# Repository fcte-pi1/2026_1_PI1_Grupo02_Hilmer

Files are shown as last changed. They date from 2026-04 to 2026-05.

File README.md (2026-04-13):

# Template PI1

Esse é o _template_ de repositório para ser utilizado pelos grupos de PI1 para organizar seu projeto. O _template_ é dividido em pastas, onde cada parte do projeto deve ser armazenada. Os arquivos a serem armazenados incluem documentação, código-fonte, arquivos de CAD, esquemáticos, arquivos de simulação de circuitos, e dados.

A organização e a correta utilização do repositório do projeto serão considerados na avaliação do grupo. Dessa forma, recomenda-se que *todos os membros* do grupo leiam as instruções deste repositório, aprendam a a utilizar o git (caso ainda não saibam) e também que o grupo combine uma estratégia de como irão utilizar o repositório em conjunto. Dessa forma não deixem de utilizar todas as ferramentas que o GitHub oferece, incluindo branchs, PRs, revisões, issues, calendários, dentre outros.

Lembrem sempre de evitar enviar arquivos muito grandes (>5MB). No caso de vídeos e outros arquivos pesados que são necessários, armazenar o arquivo em outra plataforma e colocar aqui apenas o _link_.

> [!IMPORTANT]
> A estrutura de pastas do projeto não reflete a divisão de equipes. Os membros podem e devem trabalhar nas diferentes pastas a depender da necessidade do projeto.

## Utilização

1. Crie o repositório do projeto utilizando a nomenclatura padrão no formato: `<ano>.<semestre>_PI1_Grupo<n>_<professor>`. Como um exemplo, um nome formado corretamente seria `2026.1_PI1_Grupo1_Diogo`. 

2. Crie uma equipe do projeto com a mesma nomenclatura do repositório porém com o sufixo `_Equipe`, como `2026.1_PI1_Grupo1_Diogo_Equipe`, e solicite, caso necessário, que a equipe tenha permissão de escrita no repositório do projeto.

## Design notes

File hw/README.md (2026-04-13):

# _Hardware_

Esta pasta deverá armazenar arquivos referentes a:

- Simulações de circuitos eletrônicos (alimentação, sensores, atuadores etc.): [Qucs](https://qucs.sourceforge.net/), [QSPICE](https://www.qorvo.com/design-hub/design-tools/interactive/qspice), [Fritzing](https://fritzing.org/), dentre outros.
- Esquemáticos de circuitos: [KiCad](https://www.kicad.org/), Qucs, QSPICE.
- Diagramas de bloco: [Canva](https://www.canva.com/pt_br/), [TikZ](https://tikz.net/).
- _Datasheets_ de componentes eletrônicos, microcontroladores, _shields_ Arduino, motores etc.
- Testes tabelados de circuitos: arquivos CSV, Excel.
- Imagens PNG e JPEG de resultados práticos: fotos de testes reais, gráficos de resultados etc.
- Outros arquivos referentes ao _hardware_ do projeto.

> [!WARNING]
> **Não acrescente código-fonte a esta pasta.** O código desenvolvido para microcontroladores e SOCs ([Arduino](https://www.arduino.cc/), [ESP32](https://www.espressif.com/), [Raspberry Pi](https://www.raspberrypi.com/)) deverá ser armazenado na pasta [src/firmware](https://github.com/fcte-pi1/template/tree/main/src/firmware) deste repositório.

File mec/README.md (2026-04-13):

# _Mecânica e Estruturas_

Esta pasta deverá ser utilizada para armazenar arquivos relativos ao projeto estrutural, mecanismos, materiais, estudos aerodinâmicos, equações dinâmicas, construção e manufatura, impressão 3D, e correlatos.

Os arquivos a serem incluídos, são, dentre outros:
- Arquivos CAD de peças e montagens (FCStd, STEP, etc). 
- Desenhos técnicos (pdf, etc).
- Arquivos de impressão 3D (STL, etc).
- Imagens rasterizadas e vetorizadas (eps, pdf, svg, etc).
- Documentos e estudos realizados para o projeto (markdown, LaTeX, etc).

Durante o projeto, os grupos são encorajados a realizarem estudos para o projeto de estruturas, mecanismos, aerodinamica, dentre outros, e muitos desses estudos não caberão no relatório a ser entregue. Esses estudos podem ser colocados também nessa pasta, preferencialmente utilizando markdown (.md) para facilitar a leitura em ambiente web. Lembre-se que você pode utilizar equações em formato LaTeX no markdown e não deixe de utilizar links para o material de referencia que utilizaram. Estudos bem realizados contarão de maneira positiva na avaliação das equipes, porém lembre-se que não é permitida a utilização de IA, e que esse material deve ser principalmente útil à equipe.

> [!WARNING]
> Não acrecente arquivos da parte de hardware eletrônico aqui, como arquivos de KiCAD. Estes devem ser salvos na pasta [hw](https://github.com/fcte-pi1/template/tree/main/hw) deste repositório.

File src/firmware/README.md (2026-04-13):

# _Firmware_
Esta pasta deverá armazenar arquivos referentes a:

- Código-fonte para microcontroladores e SOCs: [Arduino](https://www.arduino.cc/), [ESP32](https://www.espressif.com/), [Raspberry Pi](https://www.raspberrypi.com/), dentre outros.
- Projetos de organização destes códigos, caso utilize IDEs: [Arduino IDE](https://www.arduino.cc/en/software/), [Visual Studio](https://visualstudio.microsoft.com/pt-br/downloads/) etc.
- Arquivos de configuração: ```CMakeLists.txt``` se for usar [CMake](https://cmake.org/download/), ```Makefile``` se for usar [make](https://www.cs.colby.edu/maxwell/courses/tutorials/maketutor/) etc.

Evite incluir:
- Artefatos de compilação: os arquivos de saída compilados (binários, arquivos objeto, .hex, .elf) devem ser gerados pelo processo de compilação e não incluídos no repositório.
- Arquivos temporários/específicos do sistema operacional: Arquivos como .DS_Store (macOS) ou arquivos de configuração do editor (a menos que esteja usando uma configuração compartilhada como .editorconfig).
- Configurações pessoais: Arquivos de configuração locais específicos da máquina do desenvolvedor.

> [!WARNING]
> **Não acrescente arquivos referentes a _hardware_ nesta pasta.** Eles deverão ser armazenados na pasta [hw](https://github.com/fcte-pi1/template/tree/main/hw) deste repositório.

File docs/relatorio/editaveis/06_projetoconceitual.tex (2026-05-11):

\chapter{Projeto Conceitual do Produto}

\section{Características gerais}

\textcolor{red}{Descrever produto de forma geral. Apresentar itens teóricos sobre o projeto a serem aprofundados ou detalhados oportunamente.}

\textcolor{red}{Apresentar e explicar a Estrutura Analítica do Projeto (EAP), tomando cuidado com a legibilidade da imagem. Se necessário, coloque a EAP dentro do comando ``\textsf{\textbackslash begin\{landscape\} \textbackslash end\{landscape\}}'' para que ela seja apresentada em uma página deitada.}

\section{Estrutura}

\textcolor{red}{Apresentar desenho em CAD, indicar dimensões por lado/aresta/cota, indicar materiais utilizados e explicar o desenho e as decisões de projeto.}

\section{Descrição de \textit{hardware}}

\textcolor{red}{A descrição de \textit{hardware} no documento deve permitir que outras pessoas repliquem o produto proposto neste documento. Para isso, deve-se explicar de forma textual os principais sub-sistemas e as escolhas de projeto, além de indicar:}

\begin{itemize}
    \item \textcolor{red}{ O diagrama de blocos \cite{blockdiagram}, que oferece uma visão geral do hardware, com as principais partes do sistema e as ligações entre elas.}
    %\item A lista de materiais \cite{bom}, que facilita a montagem do sistema, indicando tudo que deve ser adquirido. Aproveitem a lista de materiais para apresentarem o orçamento dos mesmos.
    \item \textcolor{red}{ O esquemático \cite{esquematico}, que mostra as conexões elétricas entre os componentes. Deve-se indicar os componentes por nomes e símbolos, e as conexões entre eles, incluindo a pinagem dos componentes. Se o esquemático ficar muito grande, pode-se separa-lo em vários esquemáticos. A ligação em \textit{protoboard} não é considerada um esquemático adequado.}
\end{itemize}

\textcolor{red}{A Fig. \ref{fig:diagrama_blocos_e_esquematico} apresenta o diagrama de blocos e o esquemático de um circuito conversor de corrente alternada para corrente direta, a título de exemplo. Repare que o diagrama de blocos indica os subsistemas do circuito completo apresentado no esquemático.
% Comecem com o diagrama de blocos, que é mais genérico, e depois indiquem os detalhes com a lista de materiais e os esquemáticos.
}

\begin{figure}
    \centering
    
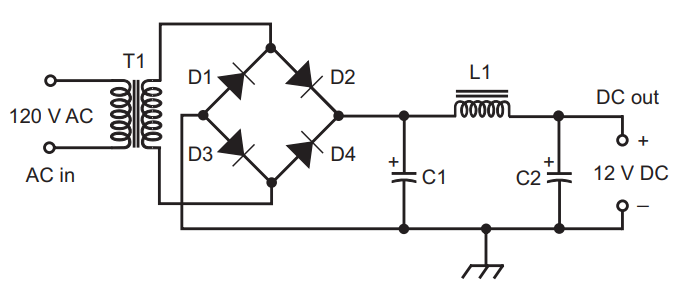
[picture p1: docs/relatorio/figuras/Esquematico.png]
    
    \caption{\textcolor{red}{Diagrama de blocos e esquemático de um circuito conversor de corrente alternada para corrente direta. Extraído de \cite{block_n_schematic}.}}
    \label{fig:diagrama_blocos_e_esquematico}
\end{figure}

\section{Análise de consumo energético}

\subsection{Identificação dos Subsistemas Elétricos}
\label{sec:identificacao_subsistemas}

A identificação dos subsistemas elétricos foi realizada com base nos componentes que consumirão energia durante a operação do micromouse, incluindo sensores, microcontroladores, atuadores, módulos de armazenamento e circuitos de suporte. Para fins de dimensionamento, foi adotado um tempo estimado de uso de 7200\,s, correspondente a uma missão de aproximadamente 2 horas. Os valores de tensão e corrente média foram obtidos a partir de \textit{datasheets} sempre que disponíveis, ou por estimativas conservadoras baseadas em condições realistas de operação.

\begin{table}[htbp]
    \centering
    \caption{Identificação dos subsistemas elétricos e parâmetros de operação}
    \label{tab:subsistemas_eletricos}

    \renewcommand{\arraystretch}{1.2}

    \begin{tabular}{lcccc}
        \hline
        \textbf{Componente} &
        \textbf{Qtde} &
        \textbf{Tensão (V)} &
        \textbf{Corrente média (mA)} &
        \textbf{Tempo (s)} \\
        \hline

        ESP32 & 1 & 3,3 & 200 & 7200 \\
        VL53L0X & 6 & 3,3 & 20 & 7200 \\
        Motor N20 (6V) & 2 & 6,0 & 400 & 7200 \\
        Driver (TB6612) & 1 & 3,3 & 30 & 7200 \\
        MPU6050 & 1 & 3,3 & 4 & 7200 \\
        INA226 & 1 & 3,3 & 0,33 & 7200 \\
        SD Reader & 1 & 3,3 & 80 & 7200 \\
        Regulador (MP1584EN) & 1 & 3,3 & 100 & 7200 \\
        Outros (LEDs, perdas) & -- & 3,3 & 100 & 7200 \\

        \hline
    \end{tabular}
\end{table}

Os valores apresentados na Tabela~\ref{tab:subsistemas_eletricos} contemplam os principais elementos energizados do sistema.

\subsection{Cálculo da Energia Consumida por Componente}
\label{sec:calculo_energia_componente}

A energia consumida por cada componente foi calculada por meio da expressão:

\begin{equation}
E = V \cdot I \cdot t
\end{equation}

em que $E$ representa a energia em joules, $V$ a tensão em volts, $I$ a corrente em ampères e $t$ o tempo de uso em segundos. Para os cálculos, as correntes em miliampères foram convertidas para ampères.

A seguir, apresenta-se o detalhamento da energia consumida por cada subsistema, cujos valores estão sintetizados na Tabela~\ref{tab:energia_por_componente}.

\begin{table}[htbp]
    \centering
    \caption{Energia consumida por componente}
    \label{tab:energia_por_componente}

    \renewcommand{\arraystretch}{1.2}

    \begin{tabular}{lc}
        \hline
        \textbf{Componente} & \textbf{Energia (J)} \\
        \hline

        ESP32 & 4752,00 \\
        VL53L0X & 2851,20 \\
        Motor N20 (2 unidades) & 34560,00 \\
        Driver (TB6612) & 712,80 \\
        MPU6050 & 95,04 \\
        INA226 & 7,84 \\
        SD Reader & 1900,80 \\
        Regulador (MP1584EN) & 2376,00 \\
        Outros (LEDs, perdas) & 2376,00 \\

        \hline
        \textbf{Total} & \textbf{49631,68} \\
        \hline
    \end{tabular}
\end{table}

\subsection{Estimativa do Consumo Total de Energia}
\label{sec:consumo_total_energia}

A energia total estimada por lançamento corresponde à soma das energias individuais dos subsistemas listados anteriormente:

\begin{equation}
E_{\text{total}}
=
4752{,}00 + 2851{,}20 + 34560{,}00 + 712{,}80 + 95{,}04 + 7{,}84 + 1900{,}80 + 2376{,}00 + 2376{,}00
\end{equation}

\begin{equation}
E_{\text{total}}
=
49631{,}68\,\mathrm{J}
\end{equation}

Para expressar esse consumo em watt-hora, utiliza-se a relação:

\begin{equation}
1\,\mathrm{Wh} = 3600\,\mathrm{J}
\end{equation}

Logo, a conversão do consumo total é dada por:

\begin{equation}
E_{\text{total,Wh}}
=
\frac{49631{,}68}{3600}
\approx
13{,}79\,\mathrm{Wh}
\end{equation}

Também é possível estimar a corrente média total do sistema a partir da soma das correntes nominais:

\begin{equation}
I_{\text{nom}}
=
200 + 120 + 800 + 30 + 4 + 0{,}33 + 80 + 100 + 100
=
1434{,}33\,\mathrm{mA}
\end{equation}

Portanto,

\begin{equation}
I_{\text{nom}}
\approx
1{,}434\,\mathrm{A}
\end{equation}

Para tornar o dimensionamento mais robusto, foi aplicada uma margem de segurança de 40\%, a fim de contemplar variações de carga, perdas não modeladas e oscilações durante a operação:

\begin{equation}
I_{\text{proj}}
=
I_{\text{nom}} \times 1{,}4
\end{equation}

Substituindo-se o valor obtido:

\begin{equation}
I_{\text{proj}}
=
1{,}434 \times 1{,}4
\approx
2{,}01\,\mathrm{A}
\end{equation}

Em seguida, considerou-se um fator de utilização de 70\%, uma vez que nem todos os subsistemas operam continuamente em máxima corrente durante toda a missão:

\begin{equation}
I_{\text{real}}
=
I_{\text{proj}} \times 0{,}7
\end{equation}

Assim,

\begin{equation}
I_{\text{real}}
=
2{,}01 \times 0{,}7
\approx
1{,}41\,\mathrm{A}
\end{equation}

A capacidade mínima da bateria pode ser estimada por:

\begin{equation}
C_{\text{min}}
=
I_{\text{real}} \times t
\end{equation}

Para uma autonomia de 2 horas:

\begin{equation}
C_{\text{min}}
=
1{,}41 \times 2
=
2{,}82\,\mathrm{Ah}
\approx
2820\,\mathrm{mAh}
\end{equation}

Para uma autonomia de 3 horas:

\begin{equation}
C_{\text{min}}
=
1{,}41 \times 3
=
4{,}23\,\mathrm{Ah}
\approx
4230\,\mathrm{mAh}
\end{equation}

\subsection{Escolha da Fonte de Alimentação}
\label{sec:escolha_fonte}

Com base no consumo energético total estimado, a demanda por lançamento é de aproximadamente 13,79\,Wh. Considerando uma margem de segurança adicional de 25\%, obtém-se uma demanda projetada de aproximadamente 17,24\,Wh.

\begin{equation}
E_{\text{proj,Wh}}
=
13{,}79 \times 1{,}25
\approx
17{,}24\,\mathrm{Wh}
\end{equation}

A fonte de alimentação selecionada é um conjunto formado por duas células idênticas em série do modelo N21700CG-50 da BAK Battery. Considerando as especificações típicas informadas, cada célula possui tensão nominal de 3,6\,V e capacidade de 5,0\,Ah. Em série, o conjunto passa a fornecer tensão nominal de 7,2\,V, mantendo a capacidade de 5,0\,Ah.

A energia nominal do conjunto é dada por:

\begin{equation}
E_{\text{bat}}
=
7{,}2 \times 5{,}0
=
36\,\mathrm{Wh}
\end{equation}

Esse valor é superior à demanda projetada de 17,24\,Wh, oferecendo folga energética suficiente para o funcionamento do robô.

Como os motores são nominais de 6\,V, o barramento principal será tratado como a alimentação de potência do sistema, enquanto os blocos de lógica, sensores e microcontrolador serão alimentados com tensão regulada pelo MP1584EN para 3,3\,V.

A tabela a seguir resume a escolha da fonte.

\begin{table}[htbp]
    \centering
    \caption{Resumo da fonte de alimentação selecionada}
    \label{tab:fonte_alimentacao}

    \renewcommand{\arraystretch}{1.2}

    \begin{tabular}{lccc}
        \hline
        \textbf{Fonte} & \textbf{Tensão nominal} & \textbf{Capacidade} & \textbf{Energia} \\
        \hline
        2 células em série & 7,2\,V & 5,0\,Ah & 36\,Wh \\
        \hline
    \end{tabular}
\end{table}

subsubsection{Síntese do dimensionamento}

Com base nos cálculos apresentados, o sistema possui consumo energético estimado de 49\,631,68\,J por lançamento, equivalente a aproximadamente 13,79\,Wh. Após aplicação de margem de segurança de 25\%, a demanda projetada passa a ser de aproximadamente 17,24\,Wh.

A fonte selecionada, composta por duas células em série, fornece aproximadamente 36\,Wh, o que atende confortavelmente à demanda do projeto. Dessa forma, a solução escolhida supre a necessidade energética do micromouse e oferece margem adequada para picos de corrente, perdas de conversão e variações operacionais.

Ressalta-se que a corrente dos motores foi considerada em regime nominal de operação, e não em condição de \textit{stall}, evitando superdimensionamento excessivo do sistema de alimentação.

\subsection{Planejamento do Circuito de Alimentação}
\label{sec:planejamento_circuito_alimentacao}

O circuito de alimentação será organizado em dois blocos: potência e lógica. O barramento principal, derivado das duas células em série, alimenta a etapa de potência, enquanto o regulador MP1584EN reduz a tensão para 3,3\,V na etapa lógica.

Para reduzir oscilações de tensão e interferências entre os subsistemas, serão adotadas as seguintes medidas:
\begin{itemize}
    \item uso de regulador buck para a linha de 3,3\,V;
    \item capacitores de desacoplamento próximos aos circuitos integrados;
    \item capacitor de bulk na entrada do sistema;
    \item separação física e elétrica entre alimentação dos motores e da lógica;
    \item uso do driver TB6612 como interface entre ESP32 e motores.
\end{itemize}

A INA226 será utilizada apenas para monitoração de corrente, tensão e potência, permitindo acompanhar o comportamento energético em tempo real. Assim, a estabilidade do sistema será garantida pela combinação entre regulação adequada, desacoplamento e separação das linhas de alimentação.

\section{Referências dos Datasheets}
\label{sec:referencias}

\begin{itemize}

    \item ESP32 -- Espressif Systems. \textit{ESP32 Series Datasheet}. Disponível em:
    \url{https://www.espressif.com/sites/default/files/documentation/esp32_datasheet_en.pdf}

    \item VL53L0X -- STMicroelectronics. \textit{VL53L0X Time-of-Flight Ranging Sensor Datasheet}. Disponível em:
    \url{https://www.st.com/resource/en/datasheet/vl53l0x.pdf}

    \item MPU6050 -- InvenSense. \textit{MPU-6000 and MPU-6050 Product Specification}. Disponível em:
    \url{https://invensense.tdk.com/wp-content/uploads/2015/02/MPU-6000-Datasheet1.pdf}

    \item TB6612FNG -- Toshiba. \textit{TB6612FNG Dual H-Bridge Motor Driver Datasheet}. Disponível em:
    \url{https://toshiba.semicon-storage.com/info/docget.jsp?did=10660}

    \item MP1584EN -- Monolithic Power Systems. \textit{MP1584 3A Step-Down Converter Datasheet}. Disponível em:
    \url{https://www.monolithicpower.com/en/documentview/productdocument/index/version/2/document_type/Datasheet/lang/en/sku/MP1584EN-LF-Z/document_id/221}

    \item INA226 -- Texas Instruments. \textit{INA226 Current/Power Monitor Datasheet}. Disponível em:
    \url{https://www.ti.com/lit/ds/symlink/ina226.pdf}

    \item BAK N21700CG-50 -- BAK Battery. \textit{Product Data Sheet}. Especificações consideradas: tensão nominal de 3,6\,V, capacidade típica de 5,0\,Ah, tensão máxima de carga de 4,2\,V, tensão final de descarga de 2,5\,V, corrente padrão de carga de 0,5C e corrente máxima de descarga de 3C.

    \item Motor N20 6V -- Especificações obtidas a partir do modelo comercial adquirido, complementadas por valores típicos de motores N20 equivalentes utilizados em aplicações embarcadas.

\end{itemize}

\section{Descrição de \textit{software}}

\textcolor{red}{Itens fundamentais:}

\begin{itemize}
    \item \textcolor{red}{ \textbf{Diagrama BPMN para entender o \textit{software} proposto:} deve deixar claro os principais atores do sistema, suas atividades (de negócios), insumos e resultados.}
    \item \textcolor{red}{\textbf{\textit{Backlog} funcional do \textit{software}:}}
    \begin{itemize}
        \item \textcolor{red}{ Escrito no formato de histórias de usuário ou casos de uso (decisão da equipe);}
        \item \textcolor{red}{ Ao declarar o \textit{backlog} de requisitos funcionais, usar a  classificação de MoSCoW (\textit{Must have}, \textit{Should have} e \textit{Could have}),  para um melhor entendimento do próprio \textit{backlog}.}
    \end{itemize}
    \item \textcolor{red}{\textbf{ \textit{Backlog} não-funcional do \textit{software}:}}
    \begin{itemize}
        \item \textcolor{red}{ Descrever os requisitos não-funcionais de forma objetiva;}
        \item \textcolor{red}{ Mais facilmente, mais rapidamente, são descrições subjetivas não-válidas. Um exemplo de requisito não-funcional de desempenho: ``a página deve carregar em até 5s quando em conexão 4G''. }
    \end{itemize}
    \item \textcolor{red}{ \textbf{Diagrama de casos de uso,} contendo os atores do sistema, os requisitos com os quais eles interagem e os tipos de relacionamentos entre requisitos realizados por um mesmo ator (ex.: \textit{include}, \textit{extend}). Obs.: este é um diagrama sobre requisitos funcionais.}
    \item \textcolor{red}{ \textbf{Descrição da arquitetura da solução de \textit{software} proposta:}}
    \begin{itemize}
        \item \textcolor{red}{ Propósito do \textit{software} (qual o seu papel no sistema);}
        \item \textcolor{red}{ Estilo arquitetural contendo:}
        \begin{itemize}
            \item \textcolor{red}{ Padrão adotado: MVC, MVP, Microsserviços, Monolítico, etc (Justificar);}
            \item \textcolor{red}{ Linguagens de programação: Java, Python, C\#, JavaScript, etc.}
            \item \textcolor{red}{ \textit{Frameworks} e bibliotecas: Spring Boot, .NET Core, React, Angular, Django, etc.}
            \item \textcolor{red}{ Banco de dados: Relacional (PostgreSQL, MySQL, etc) X NãoSQL (MongoDB,etc). }
        \end{itemize}
        \item \textcolor{red}{ Diagrama de alto nível: representação esquemática dos componentes da arquitetura, suas responsabilidades e comunicações, esclarecendo a composição do \textit{front-end} e do \textit{back-end}.}
    \end{itemize}
    \item \textcolor{red}{ \textbf{Persistência de dados:} diagrama de entidade relacionamento do banco de dados usado na solução proposta.}
    \item \textcolor{red}{ \textbf{Análise de dados:} as variáveis definidas nos requisitos do projeto em abordagem numérica e gráfica.}
    \item \textcolor{red}{ \textbf{Diagrama de estados} esclarecendo os estados assumidos pelo \textit{software} e os eventos que causam as mudanças de estado do \textit{software}.}
    \item \textcolor{red}{ \textbf{Protótipo funcional do \textit{software}, navegável.}}
    \item \textcolor{red}{\textbf{ Roteiro de testes funcionais:} }
    \begin{itemize}
        \item \textcolor{red}{Código do caso de teste;}
        \item \textcolor{red}{Nome do caso de teste;}
        \item \textcolor{red}{Tipo do caso de teste (unitário, integrado ou sistema);}
        \item \textcolor{red}{ Objetivo do caso de teste;}
        \item \textcolor{red}{ Pré-condições do sistema para o teste ser realizado;}
        \item \textcolor{red}{ Descrição dos procedimentos a serem executados para o teste;}
        \item \textcolor{red}{ Resultado esperado para o teste ser aprovado (pós-condição após realizado o teste);}
        \item \textcolor{red}{ Especificação do reparo a ser executado (caso o teste não seja aprovado);}
        \item \textcolor{red}{ Resultado após reparo (o caso do teste ser necessário de ser repetido após reparo).}
    \end{itemize}
\end{itemize}

% \textcolor{red}{Com relação ao \textit{software}, será necessário apresentar os seguintes itens: % pacotes de componentes de \textit{software}, suas funções e características, e explicar as decisões de projeto:
% \begin{enumerate}
%     \item Um diagrama do processo de negócio do problema que a máquina se propõe a resolver (BPNM) – não é UML, mas é fundamental para entender como o sistema se comporta como um todo, incluindo o usuário;
%     \item Lista de casos de uso (backlog do sistema). Backlog funcional;
%     \item Lista de requisitos não-funcionais a serem satisfeitos pelo sistema;
%     \item Diagrama de casos de uso: mostrando os requisitos funcionais, seus atores e como eles interagem entre si;
%     \item Diagrama de Classes: apresentando quais dados são manipulados pelo sistema (internamente e externamente – ex.: resultados de experimentos);
%     \item Diagrama de arquitetura, identificando todos os componentes da máquina e suas iterações com o software;
%     \item Diagrama de estados da máquina (sistema);
%     \item Descrição dos testes dos componentes da máquina e dos testes funcionais que deveriam ser feitos para avaliar o funcionamento da máquina e identificar defeitos. São importantes os testes unitários (componentes) e de integração (conjunto de componentes) e o roteiro de testes.
% \end{enumerate}
% }
%\textcolor{red}{Com relação ao \textit{software}, será necessário apresentar pacotes de componentes de \textit{software}, suas funções e características, e explicar as decisões de projeto.}

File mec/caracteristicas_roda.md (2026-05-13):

# Características da Roda e Pneu do Micromouse

## 1. Introdução

Nesse documento, estão descritas as características centrais e demais informações referentes ao modelo de roda (que inclui a roda interna e o pneu) selecionado para o projeto de micromouse, que possuirá duas rodas na parte de trás da carcaça e um deslizador (skid) na frente.

As características definidas foram baseadas em diversos fatores, os quais estão, em sua maioria, descritos na página [*Esboço de características desejáveis das rodas*](./mec/esboco_caracteristicas_desejaveis_rodas.md). Além disso, a escolha também foi influenciada pelo fato de integrantes da equipe se disporem a emprestar rodas que possuiam, com propriedades adequadas, para o projeto. Essa abordagem permite que o grupo corte o custo de compra das rodas, e dispensa o tempo necessário para a encomenda e entrega do produto.

<br>

## 2. Propriedades

### 2.1. Material

O pneu é composto de um **elastômero termoplástico (TPE)** chamado de **SBS** (*estireno-butadieno-estireno*). Esse material é conhecido pela sua flexibilidade, maciez e alta aderência, sendo essa última fundamental para o desejável alto atrito com o solo.

A roda interna, que já é moldada para o encaixe com o pneu, é feita de plástico  **ABS** (*Acrilonitrila Butadieno Estireno*), que possui boa durabilidade e resistência, além de sua leveza.

### 2.2. Dimensões

O pneu possui um diâmetro de *30 mm* e largura de *11 mm*. A roda interna, por sua vez, possui diâmetro de *17 mm* e largura de *7 mm*, além de um vão no seu eixo de 
diamêtro *4,5 mm*.

### 2.3. Textura da banda de rodagem

A textura da banda de rodagem é composta por uma linha central lisa com largura *1,94 mm*, e sulcos de comprimento *2,75 mm* em ambos os lados por toda a superfície.

Apesar de ser preferível uma superfície sem sulcos, para maximizar o atrito com a superfície lisa em *MDF*, a existência de sulcos não trará impactos negativos significantes para essa questão, dado o escopo e o contexto do projeto.

<br>

## 3. Desenhos Técnicos

Abaixo, estão apresentados os desenhos técnicos da roda interna e do pneu.

<p align="center"><i>Imagem 1:</i> Desenho técnico da Roda Interna</p>

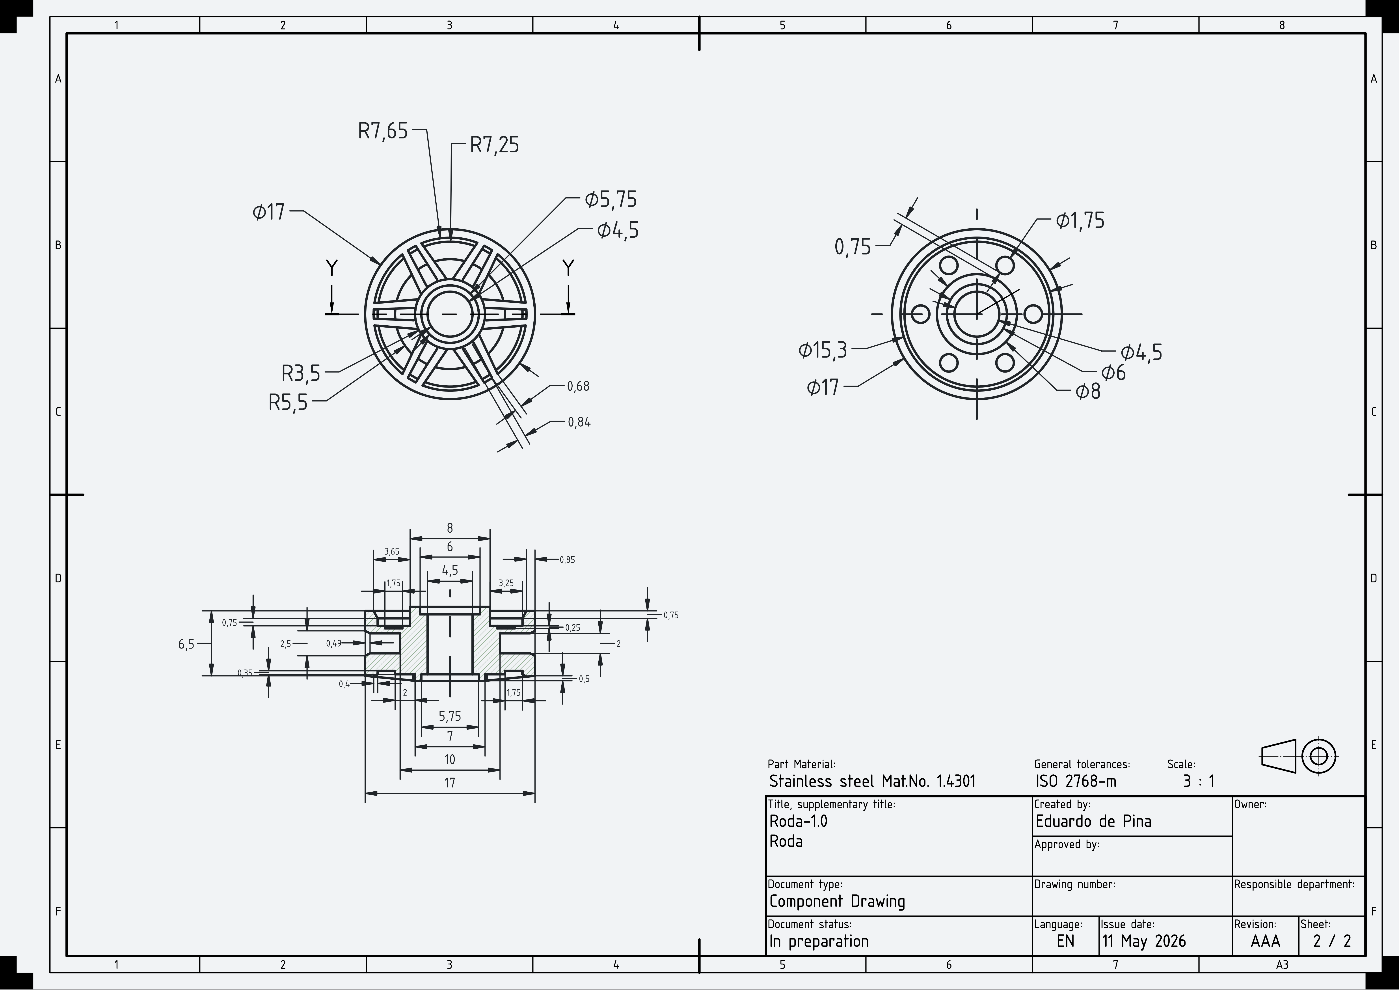
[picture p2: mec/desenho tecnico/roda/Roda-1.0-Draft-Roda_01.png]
Roda Interna


<p align="center"><b>Fonte: </b>Autoria de <a href="https://github.com/eduardodpms">Eduardo de Pina</a></p>

<br>

<p align="center"><i>Imagem 2:</i> Desenho técnico do Pneu</p>

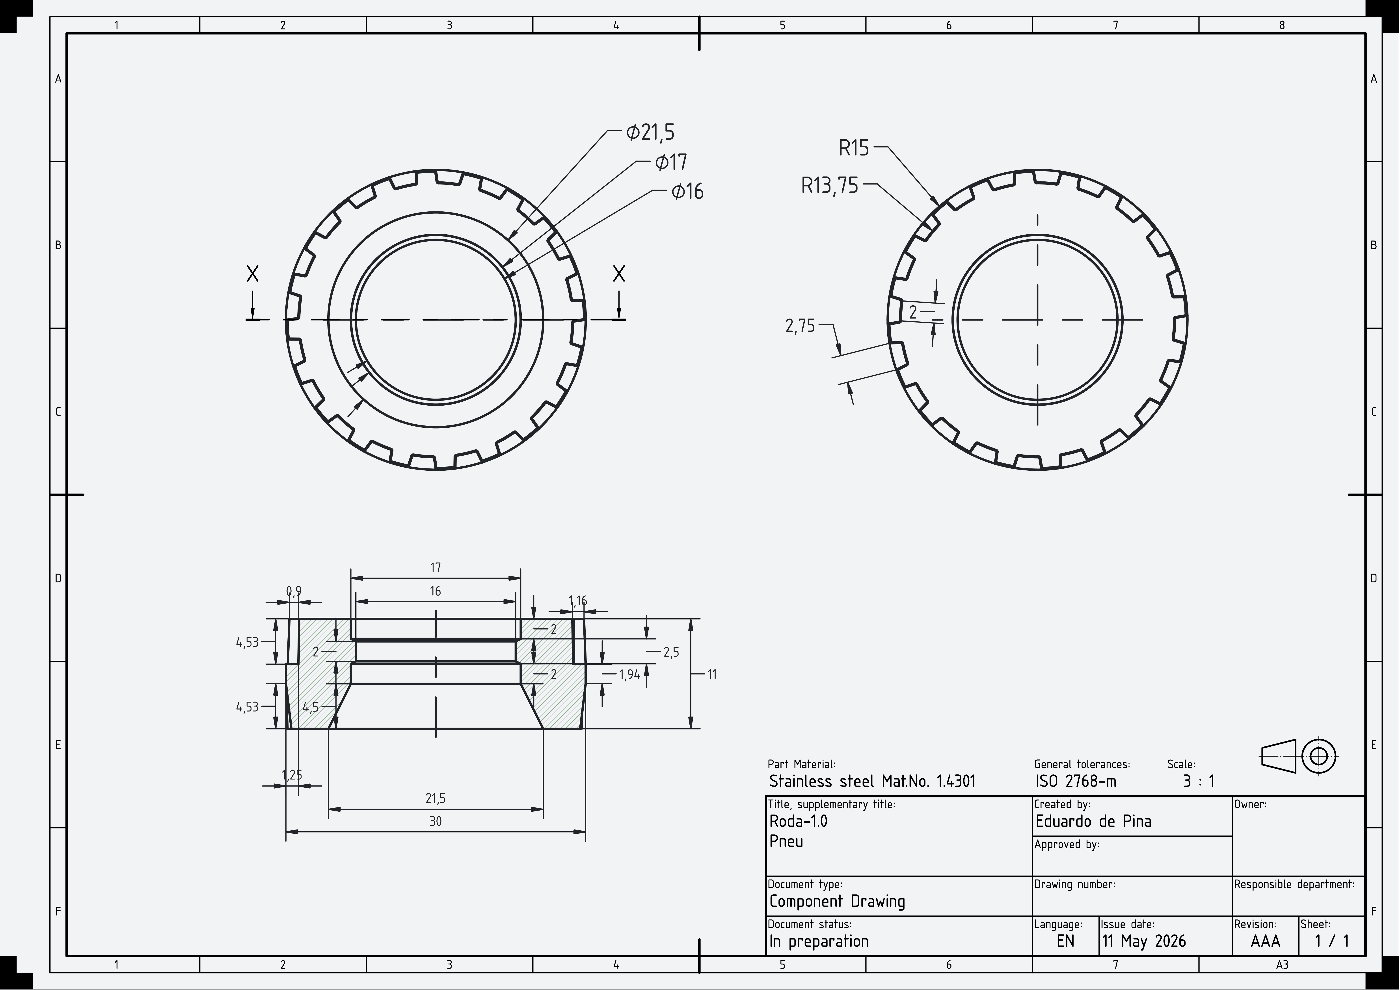
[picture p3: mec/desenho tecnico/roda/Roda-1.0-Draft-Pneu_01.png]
Pneu


<p align="center"><b>Fonte: </b>Autoria de <a href="https://github.com/eduardodpms">Eduardo de Pina</a></p>

<br>

## 4. Tabela de Versionamento

| Versão | Data | Autor | Descrição | Revisor |
| :-: | :-: | :-: | :-: | :-: |
| 1.0 | 12/05/2026 | [Eduardo de Pina](https://github.com/eduardodpms) | Criação do documento | [Giovanni Mateus](https://github.com/GiovanniMateus
) |

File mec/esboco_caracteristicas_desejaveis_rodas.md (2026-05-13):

# Esboço das características desejáveis das rodas

## 1. Introdução

Seguindo o modelo inicial de CAD para o robô desenvolvida pelo núcleo de estrutura e pesquisas direcionadas, foram discutidas medidas provisórias para serem utilizadas como base na seleção das rodas e pneus que serão utilizados no MicroMouse, buscando cumprir o objetivo da equipe.

<br>

## 2. CAD e Vãos

A base do modelo do robô está apresentada por meio de um CAD neste repositório. A imagem a seguir exibe, em vista tridimensional, uma captura de tela desse modelo.

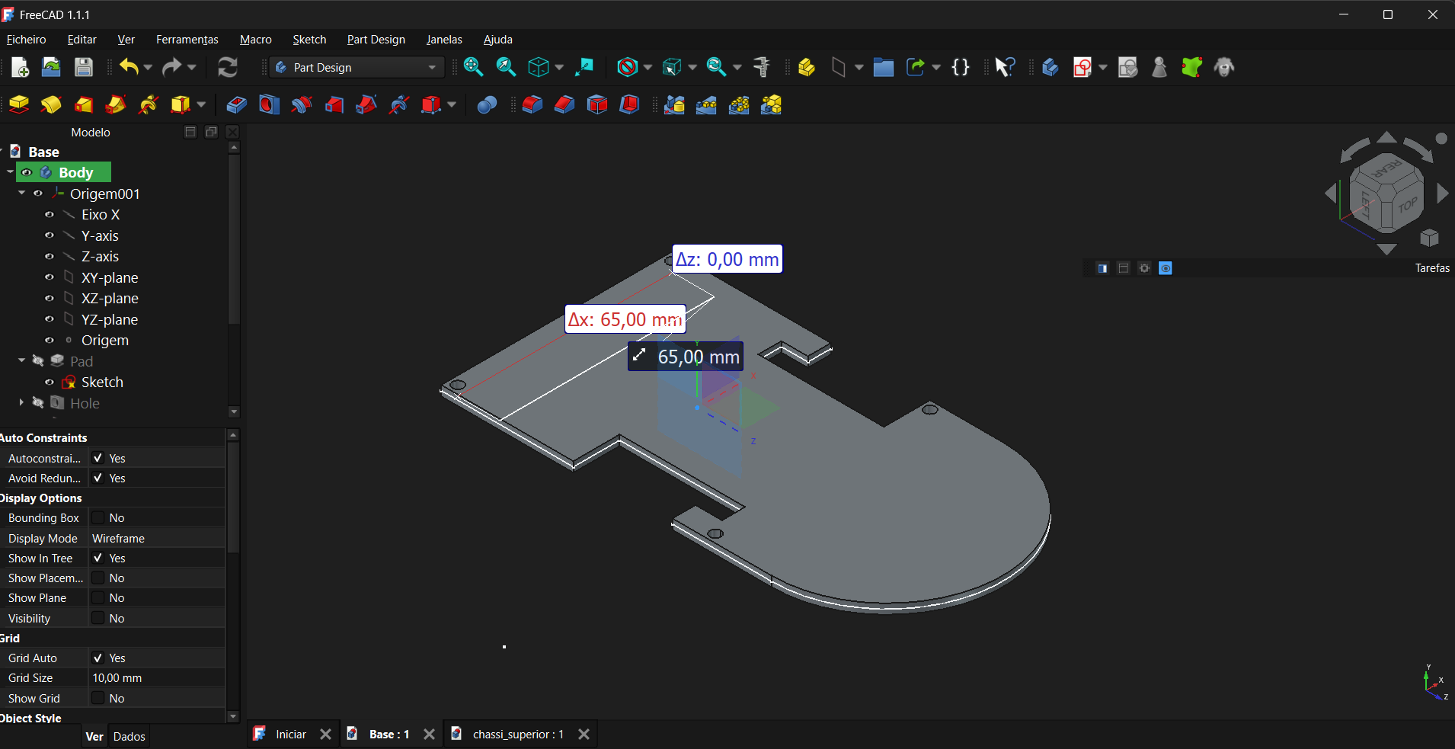
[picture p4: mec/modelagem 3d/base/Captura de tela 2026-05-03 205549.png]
CAD da Base


Os vãos destinados as rodas têm as dimensões de **30mm** x **14mm**, o que dá um direcionamento para a decisão da faixa de tamanhos possíveis para a roda.

<br>

## 3. Largura dos Pneus

A largura dos pneus, ou largura da banda de rodagem, é um fator que influencia diretamente na estabilidade do robô, assim como na precisão em curvas e no atrito com o solo. De forma resumida, para um *micromouse*, rodas mais finas proporcionam curvas mais precisas, enquanto rodas mais grossas proporcionam maior estabilidade para a estrutura como um todo, e maior área de contato do pneu com o solo, isto é, maior atrito.

Considerando o objetivo central da equipe, que não está focada em desenvolver um robô competitivo, e sim um robô estável, funcional, testável, e capaz de superar pequenos buracos de encaixe no labirinto, haverá uma preferência por rodas mais grossas (banda de rodagem > **1cm**). Além disso, há um espaço de **14mm** disponível para a roda no modelo inicial do chassi, o que não implica em um fator limitante para esse tamanho (já que uma parte do excesso pode extrapolar a largura do robô), mas dá um direcionamento nesse sentido.

Nesse sentido, a faixa ideal de largura da roda, seguindo o alinhamento da equipe, é de `11mm - 15mm`.

<br>

## 4. Diâmetro dos Pneus

O diâmetro dos pneus é outro fator decisivo na relação de escolha da roda. Rodas maiores tendem a fornecer maior velocidade em troca de mais torque, enquanto rodas menores tendem a fornecer mais precisão. Adicionalmente, aqui há um fator limitante para essa escolha: o comprimento do vão do chassi, que deve ser estritamente maior que o pneu para permitir a rolagem.

Para isso, será definida uma faixa de diâmetros de `20mm - 25mm`, que garantirá ao menos **5mm** de folga para a rolagem dos pneus, proporcionando também um tamanho que respeite a estrutura geral do *micromouse*.

<br>

## 5. Grip e Atrito

O *grip* é uma variável complexa que analisa fatores como [material](#6-material), textura e [largura dos pneus](#3-largura-dos-pneus), condições e material da pista para maximizar o atrito na superficie. Esse objetivo é central no desenvolvimento do projeto, uma vez que pneus sem atrito dificultam a previsibilidade e o cálculo dos movimentos do robô, além de também prejudicarem o controle sobre os mesmos.

Em relação às condições da pista, é esperado que a mesma seja construida sobre um material *mdf*, sem quantidades relevantes de umidade ou poeira, o que dispensa a necessidade de *sulcos* na banda de rodagem. Com relação à textura do material do pneu, o ideal seria um pneu liso, para maximizar o *grip* com o solo, mesmo essa abordagem tendendo a proporcionar maior desgaste do pneu com o tempo.

Nesse sentido, apesar de **preferível** que não haja textura na banda de rodagem, e existência de sulcos não impactará significativamente no atrito com o solo a ponto de prejudicar a equipe.

<br>

## 6. Material

Por fim, a respeito do material do pneu, é desejado um material macio e aderente. Para isso, é preferível alguma derivação de **borracha sintética**, como aquelas utilizadas nas peças de *Lego* (*SBS* e *SEBS*). Por fins de personalização, uma alternativa plástica seria o *filamento TPU*, utilizado em impressoras 3D.

<br>

## 7. Referências utilizadas

JAIN, J. **Robot Wheel Traction: Surface & Tire Type Selection Guide**. ZBOTIC. Disponível em: https://zbotic.in/robot-wheel-traction-surface-tire-type-selection-guide. Acesso em 4 maio 2026.

**How to choose proper Tires**. Micromouse USA. Disponível em: http://micromouseusa.com/?p=1111. Acesso em 4 maio 2026.

**What is The Role of Tire Size in Speed, Grip, and Stability?**. Brewminate. Disponível em: https://brewminate.com/what-is-the-role-of-tire-size-in-speed-grip-and-stability. Acesso em 4 maio 2026.

**De que são feitas as peças LEGO®?**. LEGO. Disponível em: https://www.lego.com/pt-br/service/help-topics/article/what-lego-bricks-are-made-of. Acesso em 4 maio 2026.

<br>

## 8. Tabela de Versionamento

| Versão | Data | Autor | Descrição | Revisor |
| :-: | :-: | :-: | :-: | :-: |
| 1.0 | 05/05/2026 | [Eduardo de Pina](https://github.com/eduardodpms) | Criação do documento | [Caio Venâncio](https://github.com/caio-venancio) |

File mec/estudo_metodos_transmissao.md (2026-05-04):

# Estudo sobre métodos de transmissão da roda no motor

## 1. Objetivo

Esta pesquisa compara métodos de  transmissão entre motor e roda para o micromouse, com foco em uma solução que seja simples de montar, confiável e adequada ao CAD do chassi.

## 2. Métodos avaliados

### 2.1 Roda direta no eixo do motor N20

Nesta opção, a roda é encaixada diretamente no eixo de saída do motor N20. Como o N20 já possui redução interna, o sistema fica mais simples:

```text
motor N20 com redução → roda encaixada diretamente no eixo
```

**Vantagens:**

- Menor quantidade de peças.
- Não precisa alinhar engrenagens externas.
- Não precisa tensionar correia.
- Menor chance de folga, travamento ou erro no CAD.
- Boa opção para garantir uma versão funcional do robô.

**Desvantagens:**

- Menor liberdade para alterar mecanicamente a relação de velocidade/torque.
- Se a roda for muito grande, o robô pode ficar rápido demais.
- Depende de encontrar roda compatível com eixo tipo D de 3 mm.

### 2.2 Engrenagens retas externas

Nesta opção, usa-se um pinhão pequeno no eixo do motor e uma engrenagem maior no eixo da roda:

```text
motor → pinhão pequeno → engrenagem maior → eixo da roda → roda
```

**Vantagens:**

- Permite aumentar o torque na roda.
- Permite reduzir a velocidade mecanicamente.
- Permite testar o chassi com um eixo de roda separado.
- É simples de explicar e pode ser fabricada ou comprada com peças de robótica.

**Desvantagens:**

- Exige alinhamento preciso entre pinhão, engrenagem maior e eixo da roda.
- Precisa de suporte para o eixo da roda, preferencialmente com bucha ou rolamento.
- Aumenta o número de peças e o risco de folga ou travamento.
- Os dois lados precisam ficar praticamente iguais para o robô não puxar para um lado.

### 2.3 Polias com correia GT2

Nesta opção, uma polia no motor transmite movimento para uma polia na roda usando correia dentada GT2:

```text
motor → polia pequena → correia GT2 → polia maior → eixo da roda → roda
```
**Vantagens:**

- transmissão mais suave e silenciosa;
- permite deixar o motor mais afastado da roda;
- reduz o contato direto entre engrenagens;
- permite alterar a relação de velocidade/torque trocando as polias;
- é comum em projetos de robótica e impressoras 3D.

**Desvantagens:**

- precisa de tensionamento correto da correia;
- se a correia ficar frouxa, pode pular dente;
- se ficar apertada demais, aumenta o atrito e pode forçar o motor;
- exige mais cuidado no CAD para prever ajuste de tensão;
- pode ocupar mais espaço no chassi.

---

## 3. Comparação das opções

| Critério | Roda direta no N20 | Engrenagens retas | Correia GT2 | Melhor para o grupo |
|---|---|---|---|---|
| Facilidade de montagem | Alta | Média | Média/baixa | Roda direta |
| Número de peças | Baixo | Médio | Médio/alto | Roda direta |
| Risco de desalinhamento | Baixo | Médio/alto | Médio | Roda direta |
| Ajuste de torque mecânico | Baixo | Bom | Bom | Engrenagens/GT2 |
| Necessidade de tensionamento | Não | Não | Sim | Roda direta/engrenagens |
| Chance de funcionar rápido | Alta | Média | Média/baixa | Roda direta |

---

## 4. Método escolhido: engrenagens retas

O método escolhido será a **transmissão por engrenagens retas**.

A ideia é usar:

- um **pinhão pequeno** no eixo do motor;
- uma **engrenagem maior** no eixo da roda.

Montagem básica:

```text
motor → pinhão pequeno → engrenagem maior → eixo da roda → roda
```

Esse método foi escolhido porque permite aumentar o torque, reduzir a velocidade e testar o chassi com um eixo de roda separado.

---

## 5. Como funciona

O motor gira o próprio eixo. O pinhão preso nesse eixo gira junto e movimenta a engrenagem maior. A engrenagem maior fica presa ao eixo da roda, fazendo a roda girar.

Etapas:

1. O motor gira.
2. O pinhão gira junto com o motor.
3. O pinhão move a engrenagem maior.
4. A engrenagem maior gira o eixo da roda.
5. O eixo gira a roda.

---

## 6. O que prever no CAD

O CAD precisa prever:

- posição dos dois motores;
- suporte firme para os motores;
- espaço para o pinhão;
- espaço para a engrenagem maior;
- furo ou suporte para o eixo da roda;
- bucha ou rolamento para o eixo;
- mesma distância e alinhamento nos dois lados do robô.

Como serão dois motores, a montagem deve ser simétrica:

```text
lado esquerdo: motor + pinhão + engrenagem + eixo + roda
lado direito: motor + pinhão + engrenagem + eixo + roda
```

---

## 7. Cálculos essenciais

### Relação de transmissão

```text
relação = dentes da engrenagem maior ÷ dentes do pinhão
```

Exemplo:

```text
pinhão = 10 dentes
engrenagem maior = 40 dentes

relação = 40 ÷ 10 = 4:1
```

Isso significa que o motor gira 4 voltas para a roda girar 1 volta. A roda fica mais lenta, mas com mais torque.

### RPM da roda

```text
RPM da roda = RPM do motor ÷ relação
```

Exemplo com motor de 750 RPM e relação 4:1:

```text
RPM da roda = 750 ÷ 4 = 187,5 RPM
```

---

## 8. Testes, riscos e conclusão

Antes de usar no robô completo, é necessário testar:

- se a roda gira sem travar;
- se o pinhão e a engrenagem estão alinhados;
- se não existe folga excessiva;
- se os dois lados giram de forma parecida;
- se o robô anda reto.

| Risco | Como evitar |
|---|---|
| Engrenagem travando | Ajustar distância entre motor e eixo da roda |
| Folga | Aproximar as engrenagens sem apertar demais |
| Robô andando torto | Usar peças e relações iguais nos dois lados |
| Atrito no eixo | Usar bucha ou rolamento |
| Motor desalinhando | Prender o motor com suporte firme |

---

## Referências rápidas

## Referências

CANADA ROBOTIX. N20 Micro Metal Gear Motor with Encoder. Disponível em: <https://www.canadarobotix.com/products/2846>. Acesso em: 2 maio 2026.

ROBOTSHOP. Aslong Motor DC 6V 750RPM 3mm Shaft Mini Metal Gearwheel Gear Motor N20 with Encoder Cable. Disponível em: <https://www.robotshop.com/products/aslong-motor-dc-6v-750rpm-3mm-shaft-mini-metal-gearwheel-gear-motor-n20-w-encoder-cable>. Acesso em: 2 maio 2026.

ROBOCORE. Micro Motor com Caixa de Redução 6V 750RPM com Encoder. Disponível em: <https://www.robocore.net/motor-motoredutor/micro-motor-caixa-de-reducao-6v-750rpm-com-encoder>. Acesso em: 2 maio 2026.

KHK GEARS. Gear technical reference: center distance. Disponível em: <https://khkgears.net/new/gear_knowledge/gear-nomenclature/center-distance.html>. Acesso em: 2 maio 2026.

SDP/SI. Timing belt and pulley technical information. Disponível em: <https://www.sdp-si.com/resources/elements-of-metric-gear-technology/index.php>. Acesso em: 2 maio 2026.

NSK. Bearing technical information. Disponível em: <https://www.nsk.com/products/bearings/>. Acesso em: 2 maio 2026.

UKMARS. UKMARSBot motor selection. Disponível em: <https://ukmars.org/projects/ukmarsbot/ukmarsbot-build-guide/motor-selection/>. Acesso em: 2 maio 2026.

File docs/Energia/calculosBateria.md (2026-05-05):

#  Estimativa de Consumo Energético

## Consumo nominal por componente

Valores baseados em datasheets (quando disponíveis) ou estimativas realistas de operação.

| Componente | Qtde | Corrente Unitária (mA) | Total (mA) | Fonte / Observação |
|---|---|---|---|---|
| ESP32 | 1 | 200 | 200 | Wi-Fi ativo típico |
| VL53L0X | 6 | 20 | 120 | Datasheet (~19mA típico) |
| Motor N20 (6V) | 2 | 400 | 800 | Operação com carga |
| Driver (DRV8833/TB6612) | 1 | 30 | 30 | Consumo interno |
| MPU6050 | 1 | 4 | 4 | Datasheet típico |
| SD Reader | 1 | 80 | 80 | Escrita moderada |
| Regulador (MP1584EN) | 1 | — | 100 | Perdas (~10%) |
| Outros (LEDs, perdas) | — | — | 100 | Margem técnica |

---

## Soma inicial

Corrente total nominal:

I_total = 200 + 120 + 800 + 30 + 4 + 80 + 100 + 100  
I_total ≈ 1434 mA ≈ 1.43 A

---

## Aplicação da margem de segurança

Considerando margem de 40% (variações operacionais e incertezas)

I_projeto = 1.43 A × 1.4  
I_projeto ≈ 2.00 A

---

##  Ajuste para uso real

Considerando fator de utilização de 70% (nem todos os componentes operam continuamente no máximo)

I_real = 2.00 A × 0.7  
I_real ≈ 1.40 A

---

## Cálculo da capacidade da bateria

### Para 2 horas de autonomia

Capacidade = 1.40 A × 2 h  
Capacidade ≈ 2.8 Ah ≈ 2800 mAh

---

### Para 3 horas de autonomia

Capacidade = 1.40 A × 3 h  
Capacidade ≈ 4.2 Ah ≈ 4200 mAh

---

## Resultado final

| Autonomia | Capacidade recomendada |
|---|---|
| 2 horas | 2500 – 3000 mAh |
| 3 horas | 4000 – 4500 mAh |

---

# Observação importante

A corrente dos motores foi considerada em regime nominal de operação e não em condição de stall, evitando superdimensionamento do sistema de energia.

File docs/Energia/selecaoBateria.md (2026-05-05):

# Componentes Necessários

## Baterias

### Pack Bateria Li-Ion 7,4V 2500mAh com BMS — R$ 67
Essa já vem toda montada, então não precisamos dos outros componentes caso a gente escolha ela.
[Ver produto](https://www.robocore.net/baterias-fontes/pack-bateria-li-ion-7_4v-2500mah-com-bms)

---

### Lishen LR2170 SA — R$ 15
**Especificações:** 21700 Li-ion, 3.6V, 4000mAh (12A) / 4500mAh (13.5A)
[Ver produto](https://www.alibaba.com/product-detail/2024-Grade-A-original-Lishen-LR2170SK_1601261306357.html)

> Não vamos considerar essa opção por causa do tempo de entrega nos sites disponíveis.

---

### Bateria 21700 3.7V 3000mAh Li-ion Recarregável c/ Proteção — Seven — R$ 30
**Especificações:** 21700, 3.7V, 3000mAh, com proteção, para lanterna e power bank
[Ver produto](https://m.magazineluiza.com.br/bateria-21700-3-7v-3000mah-li-ion-recarregavel-c-protecao-para-lanterna-e-power-bank-seven/p/ka5h0ggffb/cj/batr/)

---

### Bateria do Professor Renato — Sem custo
**Especificações:** Íon de lítio, 3.7V, 1500mAh
Baterias cedidas pelo laboratório do Professor Renato — opção escolhida pela equipe.

---

## Outros Componentes

| Componente | Preço Médio | Link |
|---|---|---|
| Jumper (Macho-Macho x40) | R$ 7,50 – R$ 19 | [Robocore](https://www.robocore.net/cabo/jumpers-macho-macho-x40-cabos) |
| Fita Isolante | R$ 5 | [Mercado Livre](https://www.mercadolivre.com.br/lorenzetti-10m-x-19mm-fita-isolante-antichama-proteco-para-fios-cor-preta/p/MLB28067596) |
| Conector JST PH 2 vias | R$ 15 – R$ 30 | [Mercado Livre](https://www.mercadolivre.com.br/mini-conector-jst-ph-2-vias-passo-20mm-05-conjuntos/up/MLBU1160212662) |
| Estanho para solda | R$ 10 | [Mercado Livre](https://www.mercadolivre.com.br/estanho-para-solda-40x60-080mm-tubo-10g/up/MLBU1764209073) |
| BMS 2S 20A 7,4V | R$ 20 | [Mercado Livre](https://www.mercadolivre.com.br/placa-bms-2s-20a-74v-cbalanceamento/up/MLBU3217754090) |
| Mini Carregador Lítio 2S | R$ 38 | [Robocore](https://www.robocore.net/baterias-fontes/mini-carregador-bateria-litio-2s) |

---

## Orçamentos

### Se o Professor Renato puder dar as baterias

**Opção recarregável:**
- Jumper + Fita Isolante + Estanho + Conector + BMS + Carregador
- **Total: R$ 19 + R$ 5 + R$ 10 + R$ 30 + R$ 20 + R$ 38 = R$ 122**

**Opção não recarregável:**
- Jumper + Fita Isolante + Estanho + Conector + BMS (x2 kits)
- **Total: (R$ 19 + R$ 5 + R$ 10 + R$ 30 + R$ 20) × 2 = R$ 168**

---

### Se o Professor Renato não puder dar as baterias

- Bateria 21700 Seven + Jumper + Fita Isolante + Estanho + Conector + BMS + Carregador
- **Total: R$ 30 + R$ 19 + R$ 5 + R$ 10 + R$ 30 + R$ 20 + R$ 38 = R$ 152**

---

### Se comprarmos uma bateria pronta

- Pack Li-Ion 7,4V 2500mAh com BMS + Carregador
- **Total: R$ 67 + R$ 38 = R$ 105**

---

## Conclusão

Depois de conversar com o Professor Renato, a gente optou pela **opção 1** — ele vai ceder as baterias do laboratório dele. São baterias de íon de lítio, 3.7V e 1500mAh.

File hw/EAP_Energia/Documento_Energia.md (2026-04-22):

# EAP – Energia 

Estrutura Analítica do Projeto voltada para o sistema responsável por fornecer energia ao micromouse.

---

## **1. Teoria**

Definição das necessidades energéticas do sistema e das restrições de tamanho.

- **1.1  Consumo de Energético:**  
    
    O consumo energético do sistema foi estimado a partir da soma das correntes dos componentes eletrônicos utilizados no micromouse.

    Com base no levantamento realizado, os principais componentes incluem:

    - ESP32  
    - Sensores VL53L0X  
    - Motores DC com encoder  
    - Driver DRV8833  
    - MPU-6050  
    - Regulador de tensão (MP1584EN)  

    A corrente total estimada do sistema é:

    **7453,6 mA (≈ 7,45 A)**

    Esse valor representa o consumo máximo considerando todos os componentes em operação simultânea, especialmente os motores, que são os maiores responsáveis pelo gasto energético.

    ###  Análise importante

    - Motores DC são os principais consumidores (pico alto de corrente)  
    - Sensores e microcontrolador têm consumo relativamente baixo  
    - O sistema precisa de uma fonte que suporte picos de corrente elevados, não só a média  

   ---

- **1.2 Autonomia:**  	
    
    A autonomia depende diretamente da capacidade da bateria utilizada.

    É importante garantir uma bateria com autonomia de, no mínimo:

    **2 a 4 horas**

    ### Fórmula base

    $\text{Autonomia (h)} = \frac{\text{Capacidade da bateria (mAh)}}{\text{Corrente total (mA)}}$

    ---
    
- **1.3 Dimensão e Peso:**  
    O peso estimado dos componentes eletrônicos é:

    **92 g**

    No entanto, é importante considerar que esse valor não representa o peso total do micromouse. A estrutura mecânica, rodas, chassi, fixadores e outros elementos adicionais também contribuem para o peso final do sistema.

    Assim, estima-se um acréscimo de **pelo menos 16 g**, resultando em um peso total aproximado de:

    **≈ 108 g ou mais**

    Isso é extremamente relevante porque:

    - O peso influencia diretamente o consumo energético  
    - Quanto maior o peso → maior esforço dos motores → maior corrente  
    - Afeta também a velocidade e eficiência no labirinto  

    ### Implicações no projeto

    - Escolher bateria leve é essencial  
    - Evitar componentes desnecessários  
    - Otimizar estrutura mecânica  

    ### Estimativa de dimensão dos componentes energéticos

    Para estimar corretamente a dimensão dos componentes do sistema energético, especialmente da bateria, é necessário considerar um conjunto de fatores que relacionam requisitos elétricos e restrições físicas do projeto.

    Primeiramente, deve-se conhecer o consumo total do sistema, obtido a partir da soma das correntes de todos os componentes eletrônicos. Esse valor é fundamental, pois determina a capacidade mínima que a bateria deve possuir para garantir o funcionamento adequado do micromouse.

    Além disso, é necessário definir a autonomia desejada, ou seja, o tempo durante o qual o robô deve operar sem necessidade de recarga. Mesmo sendo uma aplicação de curta duração, como a navegação em labirinto, a autonomia deve ser suficiente para testes, ajustes e múltiplas tentativas.

    Outro fator essencial é a densidade de energia da bateria, que relaciona a quantidade de energia armazenada com seu volume e peso. Esse parâmetro permite selecionar baterias que ofereçam maior capacidade ocupando menos espaço, o que é ideal para sistemas compactos como o micromouse.

    ### Fatores adicionais importantes

    - **Dimensões físicas disponíveis no chassi:**  
    O espaço interno do robô limita diretamente o tamanho máximo da bateria e dos demais componentes.  

    - **Peso máximo suportado:**  
    O aumento de peso impacta o desempenho dos motores e o consumo energético.  

    - **Formato da bateria:**  
    Diferentes formatos (retangulares, cilíndricos, tipo pouch) influenciam a facilidade de integração na estrutura.  

    - **Distribuição dos componentes:**  
    A posição da bateria afeta o centro de massa e a estabilidade do robô.  

    Por fim, deve-se garantir que a bateria escolhida seja capaz de fornecer não apenas a corrente média, mas também os **picos de corrente exigidos**, principalmente durante a aceleração dos motores.

---

## **2. Seleção**

A seleção da bateria foi feita com base na corrente total estimada do sistema (**7453,6 mA**), nas tensões exigidas pelos subsistemas (**3,3 V** para ESP32 e sensores, e **6 V** para os motores) e nas restrições de peso e espaço do micromouse.

- **2.1 Tipo de Bateria:**  
    A bateria mais adequada para o projeto é uma **Li-Po 2S (7,4 V)**.  
    Essa escolha se deve à sua **alta densidade de energia**, **capacidade de descarga elevada**, **baixo peso** e **boa compatibilidade com os reguladores do sistema**.  
    A tensão de 7,4 V também oferece margem adequada para alimentar os motores e os circuitos de 3,3 V por meio de regulação
    
- **2.2 Capacidade:**  
    A bateria deve suportar a corrente total estimada de **7,45 A** com margem de segurança.  
    Por isso, recomenda-se uma bateria entre **850 mAh e 1000 mAh**, com taxa de descarga de pelo menos **10C**, sendo **20C** a opção mais segura.

    A corrente máxima fornecida pela bateria é dada por:

    **Corrente máxima = Capacidade (Ah) × Taxa de descarga (C)**

    Exemplo:
    - **850 mAh a 20C** → até **17 A**
    - **1000 mAh a 20C** → até **20 A**

    Essa faixa atende ao sistema com folga e mantém o peso do robô reduzido.
    
- **2.3 Conector:**  
    O conector recomendado é o **XT30**, por suportar correntes elevadas com maior segurança e menor resistência de contato.  
    Isso reduz riscos de aquecimento e mau contato durante a operação do micromouse.
    
- **2.3 Preço:**  
    O preço da solução de alimentação deve considerar não apenas a bateria, mas também sua compatibilidade elétrica e mecânica com o projeto. Para isso, devem ser comparados modelos reais quanto à tensão, capacidade, taxa de descarga, peso, dimensões, tipo de conector incluído e custo de carregamento. Caso a bateria já possua conector compatível com o sistema, esse item não gera custo adicional; caso contrário, deve-se considerar o uso de adaptadores ou a substituição do conector. Assim, o critério de preço deve ser analisado com base no custo total de integração da solução energética.
	
---

## **3. Projeto**

Intercessão com a eletrônica necessária para transformar a bateria selecionada em um sistema de alimentação **funcional, seguro e utilizável** no micromouse. Essa etapa inclui o desenvolvimento do **circuito de carregamento e dos mecanismos de proteção elétrica**, garantindo operação estável e segura. Sua importância está na transição entre a definição teórica da fonte de energia e sua implementação prática, assegurando a integridade dos componentes eletrônicos e a confiabilidade do sistema como um todo.

- **3.1 Carregador:**  
    - Definição do método de carregamento (USB, módulo TP4056, etc.)
    - Circuito de recarga implementado
    - Especificação de corrente e tensão de carga, regido pelo regulador de tensão (provavelmenete MP1584EN)
  
    A importância desse módulo é garantir que a bateria seja **carregada corretamente e com segurança**, evitando a sobrecarga e a degradação precoce da bateria, assim, permitindo reutilização contínua do micromouse.
    
- **3.2 Proteção Contra Curto:**  
    - Sistema de proteção implementado:
        - Fusível (o mais provável) ou
        - BMS ou
        - Circuito de proteção equivalente
    - Definição de limites de corrente

    Uma das partes mais críticas do projeto, pois **protege contra curto-circuitos e sobrecorrentes**, assim evitando dano ao MCU, aos motores e até possíveis danos a estrutura do micromouse

---

## **4. Integração**

Incorporação física e validação do sistema de energia.

- **4.1 Acoplamento da Estrutura:**  
	Esta atividade define o método de fixação física da bateria Li-Po 2S e dos demais componentes do sistema de energia ao chassi do micromouse, equilíbrio de massa e facilidade de manutenção.

	**Posicionamento da Bateria**

	 É preferível posicionar a bateria de forma centralizada no eixo longitudinal do robô, preferencialmente entre os dois motores, próxima ao centro de massa do conjunto. Isso minimiza o momento de inércia durante as curvas no labirinto e reduz o esforço compensatório dos motores. Vale ressaltar que caso algum componente seja sensível a temperatura, este não deve permanecer próximo a bateria ou vice versa.

	**Método de Fixação**

	Com base em outros micromouses usados para competição, os métodos mais utilizados são tanto colar diretamente a bateria no micromouse, como também o uso de encaixes fixados nele. A primeira opção é mais fácil de ser implementada, é mais barata, mas dificulta a manutenção. Já a segunda tem uma melhor manutenção ao custo de ser mais difícil de ser implementada.
    
- **4.2 Conexões dos Cabos:**  
    Esta atividade foca-se na definição da infraestrutura de cablagens necessária para suportar a corrente de pico de 7,45 A, integrando os componentes do projeto:

    - Dimensionamento de Condutores: Definir a bitola adequada para os cabos de potência que ligarão a bateria aos drivers de motor, garantindo que a resistência não comprometa o torque dos motores N20.

    - Implementação do Conector XT30: Montagem do conector XT30 de forma a assegurar uma ligação robusta e de baixa resistência entre a bateria Li-Po e o circuito principal.

    - definir o posicionamento físico e o método de instalação do fusível de vidro (previsto na planilha) para garantir que este atue eficazmente antes de qualquer dano ao ESP32 ou aos drivers.

    - Organizar o chicote elétrico para alimentar os 6 sensores VL53L0X e o MPU-6050, minimizando a desordem de cabos e interferências no chassi.

- **4.3 Telemetria da Energia:**
Esta etapa tem como objetivo implementar um sistema de monitoramento em tempo real do consumo energético do micromouse, permitindo análise de desempenho e validação de autonomia.

  **Objetivos de Medição**

  Para atender às necessidades do projeto e validar os requisitos definidos nas seções anteriores, o sistema de telemetria deve medir:

  -   **Corrente (A)**
    Utilizada para validar a estimativa de consumo total (**7,45 A**) e identificar picos de corrente dos motores, que são importantes para o dimensionamento da bateria e da proteção contra sobrecorrente.
  -   **Tensão (V)**
    Necessária para verificar a estabilidade da alimentação, especialmente nas linhas de **3,3 V**, garantindo funcionamento correto do sistema eletrônico.
  -   **Potência (W)**
    Permite analisar o consumo instantâneo do sistema, correlacionando diretamente com o esforço dos motores e o comportamento dinâmico do micromouse.
  -   **Energia consumida (Wh)**  
    Fundamental para validar a autonomia real do sistema, comparando os resultados experimentais com a estimativa teórica baseada na capacidade da bateria.

  **Sensor Selecionado**

  O sensor escolhido para essa aplicação é o **INA226**, por apresentar melhor desempenho em relação a outras alternativas como o **INA219** pelo mesmo valor.

  **Características principais**

  -   **Medição de**:
      -   Corrente
      -   Tensão
      -   Potência (diretamente pelo hardware)
  -   **Alta precisão (16 bits)** → melhor resolução para análise detalhada
  -   **Comunicação via I2C (digital)** → fácil integração com o ESP32
  -   **Shunt digital integrado** → simplifica o circuito de medição
  -   **Baixo custo**:
      -   ~R$15 (importação)
      -   ~R$30 (mercado nacional)

  **Cálculo de Energia**

  A energia consumida não é medida diretamente pelo sensor, mas pode ser obtida via integração da potência ao longo do tempo:

  $E(Wh) = \int P(t)\, dt$

   Na prática, isso será implementado no ESP32 via amostragem discreta:
  -   Leitura periódica da potência
  -   Soma acumulada ao longo do tempo
	
- **4.4 Testes Finais:**  
    Esta etapa tem como foco garantir o bom funcionamento assim como a segurança operacional da distribuição elétrica:

    - Validação de Autonomia: O sistema precisa de ser testado em operação contínua para confirmar se a configuração final suporta o requisito de 2 a 4 horas de funcionamento no labirinto.

    - Monitorização de Estabilidade (Ripple): É necessário validar, através de medições, se a oscilação de tensão na linha lógica permanece abaixo do limite estabelecido de 30mV, assegurando a integridade do SD Reader e dos sensores.

    - Ensaio de Resiliência Mecânica: O protótipo precisa de ser submetido a manobras de alta aceleração e travagens bruscas para validar se o método de conexão e fixação dos cabos suporta o esforço mecânico sem interrupções de energia.

    - Avaliação Térmica do Regulador: É necessário monitorizar a temperatura do regulador MP1584EN sob carga máxima para definir se a dissipação térmica natural é suficiente para a autonomia pretendida ou se requer ajustes.

---

## Versionamento

| Versão | Data | Descrição | Autor(es/as) |
| :--- | :--- | :--- | :--- |
| 0.1 | 17/04/2026 | Estruturação do documento de EAP escrito | João Maurício |
| 0.2 | 19/04/2026 | Especificação da seção "Projeto" | João Maurício |
| 0.3 | 19/04/2026 | Especificação da seção "Teoria" | Giovanna Aguiar |
| 0.4 | 19/04/2026 | Especificação da seção de "Seleção" | Tiago Balieiro |
| 0.5 | 19/04/2026 | Especificação parcial da seção "Integração" | Cristiano Morais |
| 1.0 | 20/04/2026 | Especificação final da seção "Integração" | Rafael Melatti |
| 1.1 | 21/04/2026 | Correção na sessão "Teoria" | Giovanna Aguiar |

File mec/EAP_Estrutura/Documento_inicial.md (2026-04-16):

# EAP - Estruturas

## 1. Labirinto

### 1.1 Piso

#### 1.1.1 Lado superior

##### Materiais
- Placa de MDF 72cm x 72cm  
- Lixa de granulometria adequada para MDF  
- Tinta preto fosco  
- Verniz fosco (se necessário)

##### Atividades

**Placas (primeira etapa)**
- CAD do piso (permitindo encaixes das paredes modulares no piso)
- Orçamento de placas de MDF
  - Encomendar a placa de MDF do tamanho adequado
  - Checar o tamanho da placa
    - Reencomendar caso não seja apropriada

**Lixamento (segunda etapa)**

**Tintas (terceira etapa)**
- Pesquisa de tintas apropriadas para MDF
- Orçamento das tintas
- Encomenda das tintas
- Pintura do lado superior com tinta preta fosca
- Checar necessidade de verniz
  - Aplicar verniz fosco, se necessário

---

#### 1.1.2 Lado inferior

##### Materiais
- Placa de MDF ou MDP 72cm x 72cm
- Lixa de granulometria adequada
- Tinta preto brilhante
- Verniz brilhante (se necessário)

##### Atividades

**Lixamento (primeira etapa)**

**Tintas (segunda etapa)**
- Pesquisa de tintas apropriadas
- Orçamento das tintas
- Encomenda das tintas
- Pintura com tinta preta brilhante
- Checar necessidade de verniz
  - Aplicar verniz brilhante, se necessário

---

### 1.2 Paredes internas

#### Materiais
- MDF ou MDP
- Lixa de granulometria adequada
- Tintas:
  - Branco
  - Vermelho

#### Atividades

**CAD das paredes modulares (primeira etapa)**
- Selecionar programas que permitam desenhos técnicos (DXF, SVG, AI, EPS)
- Realizar o CAD das paredes:
  - Encaixe entre paredes
  - Encaixe no piso
  - Auto sustentação
  - Dimensões: 5cm de altura e 18cm de comprimento

**Recorte do MDF (segunda etapa)**
- Orçamentos
- Encomenda de pelo menos 24 placas (15mm de espessura)
- Verificação das especificações técnicas

**Pintura (terceira etapa)**

*Lateral*
- Lixar levemente
- Pintura com tinta branca
- Aplicar verniz, se necessário

*Superior*
- Lixar levemente
- Pintura com tinta vermelha
- Aplicar verniz, se necessário

---

### 1.3 Paredes externas

#### Materiais
- MDF ou MDP
- Lixa de granulometria adequada
- Tintas:
  - Branco
  - Vermelho
- Verniz (se necessário)

#### Atividades

**CAD das paredes modulares (primeira etapa)**
- Selecionar programas compatíveis (DXF, SVG, AI, EPS)
- Realizar o CAD das paredes:
  - Encaixe entre paredes
  - Encaixe no piso
  - Auto sustentação
  - Dimensões: 5cm de altura e 72cm de comprimento

**Recorte do MDF (segunda etapa)**
- Orçamentos
- Encomenda de pelo menos 4 placas (15mm de espessura)
- Verificação das especificações técnicas

**Pintura (terceira etapa)**

*Lateral*
- Lixar levemente
- Pintura com tinta branca
- Aplicar verniz, se necessário

*Superior*
- Lixar levemente
- Pintura com tinta vermelha
- Aplicar verniz, se necessário

---

## 2. Micromouse

### 2.1 Material
- Pesquisa de material e orçamento

### 2.2 Distribuição de pesos e estabilidade

### 2.3 Rodas

### 2.4 Estrutura de sustentação da placa

### 2.5 Modelagem CAD
- Componentes com estruturas de encaixe
- Arquivo com as visões de cada peça

### 2.6 Ilustração do carro em CAD
- Junção de componentes e simulação
- Vista explodida

---
## Documento

[EAP_estruturas.pdf](https://github.com/user-attachments/files/26782925/EAP_estruturas.pdf)

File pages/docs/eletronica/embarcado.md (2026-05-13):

## Backlog do Produto

O *Backlog* do Produto consolida as necessidades e funcionalidades do sistema Micromouse, sendo estruturado para garantir a rastreabilidade e a priorização adequada das entregas. As funcionalidades do sistema foram documentadas diretamente utilizando-se a técnica de Histórias de Usuário (HU), permitindo a compreensão clara das necessidades dos atores sob a perspectiva de valor de negócio.

Para a priorização dos itens, adotou-se o método MoSCoW, classificando as funcionalidades em *Must Have* (essenciais), *Should Have* (importantes, mas não vitais) e *Could Have* (desejáveis). Adicionalmente, os requisitos não-funcionais (RNF) foram definidos sob critérios objetivos, evitando descrições subjetivas e focando em métricas mensuráveis de desempenho, como tempo de resposta e estabilidade da conexão.

Todas as Histórias de Usuário (HUs) possuem descrição estruturada no formato **Eu–Como–Para**, critérios de aceitação e protótipos de interface devidamente documentados. A estrutura completa do Backlog do Produto encontra-se disponível no [Backlog do Projeto no GitHub](https://github.com/orgs/fcte-pi1/projects/16/views/1), permitindo rastreabilidade e acompanhamento detalhado do desenvolvimento do projeto.

Vale ressaltar que este documento foca nos épicos e requisitos relacionados ao desenvolvimento de sistemas **Embarcados**. A parte complementar do backlog, com foco no sistema web e gerenciamento de dados, pode ser encontrada na seção de [Software](../software/backlog-produto.md).

As tabelas a seguir apresentam a divisão do backlog organizada por épicos de desenvolvimento.

---

### Épico A: Desenvolvimento de Firmware

| ID | Título da História | Priorização (MoSCoW) | História de Usuário | Critério de Aceite |
| :---- | :---- | ----- | :---- | :---- |
| **HU-02** | Percepção e Segurança | Must Have | Eu como avaliador, desejo que o circuito tenha sensores de distância e proteções elétricas, para que o robô detecte paredes sem sofrer danos. | **CA-02-01**:Sensores IR devem detectar objetos a pelo menos 30 cm. **CA-02-02**:PCB com proteção contra curto-circuitos para prevenir danos ao MCU. **CA-02-03**:Sistema de sensores deve cobrir angulação de pelo menos 90°. |
| **HU-03** | Controle e Energia | Must Have | Eu como sistema embarcado, quero processar os sinais dos encoders e sensores inerciais, para que o Micromouse execute movimentos precisos. | **CA-03-01:** O sistema deve converter os pulsos dos encoders em velocidade linear e angular do robô **CA-03-02:** O sistema deve atualizar continuamente a posição estimada do robô com base na odometria **CA-03-03:** O sistema deve utilizar dados do acelerômetro para detectar impactos ou desvios de trajetória **CA-03-04:** O sistema deve ajustar o controle de movimento para manter a trajetória desejada durante a navegação |
| **HU-04** | Persistência de Dados | Should Have | Eu como desenvolvedor, quero que o robô armazene a telemetria em um cartão SD, para garantir que os dados não sejam perdidos. | **CA-04-01**:Gravar dados em tempo real no SD Card em formato CSV ou JSON. **CA-04-02**:Garantir a integridade do arquivo mesmo se a alimentação for interrompida bruscamente |
| **HU-06** | Energização e Bateria | Must Have | Eu como avaliador, quero que o sistema de energia permita recarregar a bateria e forneça alimentação estável. | **CA-06-01**: O sistema deve iniciar a recarga automaticamente ao ser conectado a uma fonte de energia externa compatível. **CA-06-02:** A conexão física deve ser robusta o suficiente para suportar múltiplos ciclos de conexão/desconexão sem perda de contato. **CA-06-03**: O sistema deve fornecer tensões constantes (ex: 3.3V, 5V, 12V) independentemente da queda gradual de tensão da bateria principal (enquanto houver carga). |
| **HU-07** | Unificação do Sistema | Must Have | Eu como avaliador, desejo que todos os subsistemas estejam integrados em uma única plataforma funcional. | **CA-07-01**: O firmware principal deve ser capaz de gerenciar simultaneamente a leitura dos sensores e o controle dos motores sem travamentos. **CA-07-02**: Os dados de telemetria coletados devem refletir com precisão o estado real de todos os sensores integrados. **CA-07-03**: A integração física de todos os componentes na PCB não deve apresentar interferências eletromagnéticas que comprometam o funcionamento do sistema. |

### Épico E: Envio de Dados de Telemetria

| ID | Título da História | Priorização (MoSCoW) | História de Usuário | Critério de Aceite |
| :---- | :---- | ----- | :---- | :---- |
| **HU-20** | Comunicação Micromouse | Must Have | Eu como avaliador quero que o sistema web se comunique com o micromouse para obter dados. | **CA-20-01: Dado** que o micromouse e o sistema estão ligados. Quando a comunicação for iniciada; Então o sistema web e o micromouse devem estabelecer uma sessão de conexão. |
| **HU-22** | Aglutinação de Dados | Must Have | Eu como avaliador, quero que o sistema organize e formate os dados de telemetria em pacotes estruturados para envio sem fio. | **CA-22-01**: O sistema deve agrupar as leituras dos sensores IR, encoders e IMU em uma única estrutura de dados (struct) ou string formatada. **CA-22-02:** A formatação dos dados deve ser compatível com a transmissão via protocolos sem fio suportados pelo ESP-32 (como UDP/TCP via WiFi ou Serial Bluetooth). |

### Épico F: Corrida para a Chegada

| ID | Título da História | Priorização (MoSCoW) | História de Usuário | Critério de Aceite |
| :---- | :---- | ----- | :---- | :---- |
| **HU-05** | Calibração de Sensores | Must Have | Eu Como avaliador, desejo que o robô realize uma calibração automática de seus sensores de luminosidade antes do início da prova, para que as variações de luz do ambiente não interfiram na precisão da leitura durante a navegação. | **CA-05-01**:Executar calibração automática de luz ambiente antes da largada. **CA-05-02**:Recalcular posição com erro máximo de \+/- 1 cm após derrapagem. |
| **HU-23** | Aglutinação de Dados em formato Enviável | Must Have | Eu Como avaliador, desejo que o robô identifique e corrija desvios de posição causados por colisões ou derrapagens, para que o mapeamento não seja corrompido e a navegação continue de forma precisa. | - |

### Histórias de Usuário Adicionais

| ID | Título da História | Priorização (MoSCoW) | História de Usuário | Critério de Aceite |
| :---- | :---- | ----- | :---- | :---- |
| **HU-01** | Exploração Autônoma | Must Have | Eu Como avaliador, desejo que o robô mapeie e resolva o labirinto de forma autônoma, para que ele alcance o objetivo central de forma eficiente. | **CA-01-01**:Utilizar algoritmo *Frontier-based Exploration* para achar a célula final. **CA-01-02**:Detectar e trocar de algoritmo ao alcançar o centro. **CA-01-03**:Utilizar *Flood Fill* para mapear a área. **CA-01-04**:Evitar loops infinitos armazenando células visitadas. |

### **Requisitos Não-Funcionais de Embarcados**

| ID | Descrição do Requisito Não Funcional | Priorização (MOSCOW) | Rastreabilidade |
| :---- | :---- | ----- | :---- |
| **RNF-01-EMB** | O sistema deve possuir sensores capazes de detectar objetos a pelo menos de 30 cm de distância. | Must Have | HU-02 |
| **RNF-02-EMB** | O sistema de sensores deve detectar objetos com angulação de pelo menos 90° com o robô parado. | Must Have | HU-02 |
| **RNF-03-EMB** | O micromouse não deve exceder 10 cm de largura ou comprimento. | Must Have | HU-01 |
| **RNF-04-EMB** | O robô não pode causar danos às paredes ou ao chão do labirinto. | Must Have | HU-02 |
| **RNF-05-EMB** | O algoritmo deve ser capaz de recuperar a posição do robô caso ocorra uma leve colisão ou derrapagem. | Should Have | HU-05 |
| **RNF-06-EMB** | O sistema deve utilizar o algoritmo frontier-based exploration para encontrar a célula final. | Must Have | HU-01 |
| **RNF-07-EMB** | O sistema deve utilizar o algoritmo Flood Fill para mapear toda a área explorável. | Must Have | HU-01 |
| **RNF-08-EMB** | O código deve ser modular para facilitar ajustes rápidos. | Should Have | HU-05/HU-07 |

## Histórico de Versões

|Versão|Data|Autor|Descrição|Revisor |
|---|---|---|---|---|
|1.0|13/05/2026|[Enzo Emir](https://github.com/EnzoEmir)|Criação do documento| -|

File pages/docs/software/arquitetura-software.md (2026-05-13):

# Arquitetura de Software

## 1. Visão Geral

O Sistema Web do Micromouse tem como objetivo apoiar o monitoramento, armazenamento e análise dos dados gerados durante as corridas do robô. A solução é responsável por receber dados de telemetria enviados pelo Micromouse, exibir informações em tempo real, persistir resultados das execuções e permitir consultas posteriores.

A arquitetura proposta utiliza uma estrutura monolítica em camadas, adequada ao escopo acadêmico do projeto, separando responsabilidades entre interface web, backend, persistência de dados, comunicação em tempo real e integração com o sistema embarcado.

---

## 2. Propósito do Software

O software atua como camada de apoio ao sistema físico do Micromouse, permitindo que os dados da corrida sejam visualizados, registrados e analisados.

As principais responsabilidades do sistema são:

- receber dados de telemetria do Micromouse;
- validar os dados recebidos;
- exibir informações da corrida em tempo real;
- mostrar indicadores como trajeto, bateria, velocidade média, tempo e status da corrida;
- persistir os dados finais da execução;
- permitir consultas históricas por labirinto;
- permitir consultas gerais das execuções.

---

## 3. Padrão Arquitetural Adotado

A solução adota uma arquitetura monolítica em camadas, composta por:

- Camada de Apresentação;
- Camada de Aplicação;
- Camada de Persistência;
- Mecanismo de Comunicação em Tempo Real.

---

### 3.1 Camada de Apresentação

Responsável pela interface web desenvolvida em React.

### Funções principais

- exibição da telemetria em tempo real;
- visualização do mapa do labirinto;
- apresentação de indicadores da corrida;
- consulta de resultados históricos.

---

### 3.2 Camada de Aplicação

Responsável pelo backend desenvolvido em FastAPI.

### Funções principais

- recebimento da telemetria;
- validação dos dados;
- gerenciamento das sessões de corrida;
- disponibilização de APIs REST;
- distribuição de eventos em tempo real para o frontend.

---

### 3.3 Camada de Persistência

Responsável pelo armazenamento dos dados no PostgreSQL.

### Funções principais

- persistência das corridas;
- armazenamento de telemetria histórica;
- armazenamento dos labirintos;
- consulta de execuções anteriores.

---

### 3.4 Comunicação em Tempo Real

A atualização em tempo real ocorre utilizando WebSocket entre backend e frontend.

O Micromouse envia os dados de telemetria ao backend via HTTP/REST através da rede Wi-Fi. Após validação, o backend redistribui os dados ao frontend utilizando WebSocket.

A atualização visual ocorre em tempo real, enquanto a persistência no banco pode ocorrer em lote para reduzir overhead de escrita.

---

### 3.5 Justificativa Arquitetural

A arquitetura foi escolhida por apresentar:

- menor complexidade de implantação;
- facilidade de desenvolvimento em equipe;
- adequação ao escopo acadêmico;
- suporte adequado à telemetria em tempo real;
- facilidade de manutenção.

Não foram adotadas arquiteturas baseadas em microsserviços devido ao aumento desnecessário da complexidade operacional para o tamanho atual da solução.

---

## 4. Tecnologias Utilizadas

### 4.1 Linguagens

| Camada | Linguagem |
|---|---|
| Frontend | JavaScript |
| Backend | Python |
| Banco de Dados | SQL |
| Firmware | C/C++ |

---

### 4.2 Frameworks e Tecnologias

| Tecnologia | Uso |
|---|---|
| React | Interface web |
| FastAPI | API backend |
| WebSocket | Comunicação em tempo real |
| PostgreSQL | Persistência de dados |
| Uvicorn/ASGI | Execução da aplicação FastAPI |
| ESP-IDF | Desenvolvimento do firmware |
| FreeRTOS | Gerenciamento de tarefas embarcadas |

---

## 5. Organização Geral da Solução

A solução é composta pelos seguintes elementos:

- Micromouse;
- Frontend Web;
- Backend FastAPI;
- Banco PostgreSQL.

---

## Fluxo Principal

1. O Micromouse coleta informações dos sensores.
2. O firmware organiza os dados de telemetria.
3. O Micromouse envia os dados ao backend via HTTP/REST utilizando Wi-Fi.
4. O backend valida os pacotes recebidos.
5. O backend redistribui os dados ao frontend utilizando WebSocket.
6. O frontend atualiza a interface em tempo real.
7. O backend persiste os dados históricos no PostgreSQL.
8. O usuário pode consultar execuções anteriores.

---

## 6. Visões Arquiteturais

A arquitetura do sistema é documentada utilizando uma adaptação do modelo 4+1.

Neste projeto, a visão de casos de uso foi substituída por uma visão de dados, conforme orientação da disciplina.

---

### 6.1 Visão Lógica

A visão lógica descreve os principais módulos da solução de software e suas responsabilidades.

Os módulos principais são:

- **Interface Web:** exibe dados de monitoramento e telas de consulta;
- **Módulo de Telemetria:** recebe e valida os dados enviados pelo Micromouse;
- **Módulo de Monitoramento:** atualiza a interface em tempo real;
- **Módulo de Persistência:** armazena os dados finais das corridas;
- **Módulo de Consulta:** permite visualizar resultados históricos.

### 6.1.1 Comportamento Dinâmico (Diagrama de Estados)

O comportamento do sistema durante o ciclo de uma corrida é regido por estados que garantem a integridade da telemetria e o controle da sessão. O fluxo transita desde a configuração inicial até o salvamento final dos dados no PostgreSQL.

Ele contempla estados como:

- aguardando configuração;
- sessão iniciada;
- aguardando largada;
- mapeamento inicial;
- conexão perdida;
- mapa consolidado;
- cálculo de rota otimizada;
- execução da rota otimizada;
- alerta crítico;
- desafio cumprido;
- desafio não cumprido;
- salvamento dos dados;
- corrida finalizada.

Esse diagrama auxilia na compreensão do comportamento dinâmico do sistema e dos eventos que provocam transições entre estados.

<p style="text-align: center;">
  <em>Figura 2: Diagrama de Estados</em>
</p>

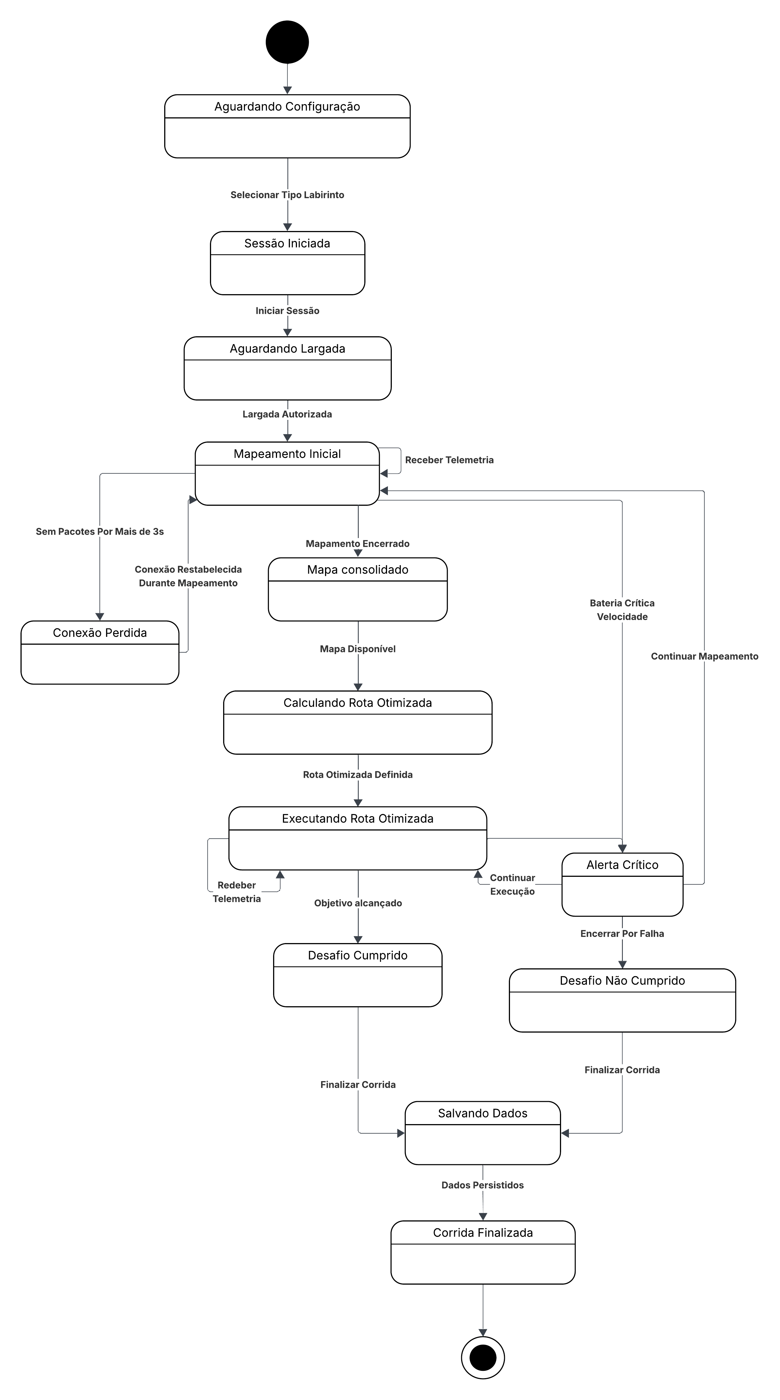
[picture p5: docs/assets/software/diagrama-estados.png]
Diagrama de Estados


<div style="text-align: center;">Autor: <a href="https://github.com/Potatoyz908">Euller</a></div>

### 6.1.2 Fluxo Operacional (Diagrama de Atividades UML)

O Diagrama de Atividades detalha o comportamento funcional e a coordenação entre o sistema embarcado e a interface de monitoramento, evidenciando a lógica de controle e o processamento de dados.

#### Estrutura do Diagrama

O fluxo utiliza **Raias (swimlanes)** para delimitar as responsabilidades entre os dois atores principais:

*   **Micromouse (Embarcado):** Responsável pela execução do algoritmo de navegação (Flood Fill), coleta de dados sensoriais (bateria, velocidade, sensores) e transmissão de telemetria.
*   **Sistema Web:** Responsável pela orquestração da sessão, validação de pacotes, interface de usuário e persistência de dados no PostgreSQL.

#### Descrição Detalhada das Atividades

1.  **Início e Decisão de Sessão:** O processo inicia no Sistema Web com a seleção do tipo de labirinto. Um **nó de decisão** garante que a sessão só avance se o labirinto for selecionado e a sessão iniciada corretamente.

2.  **Paralelismo no Micromouse:** Após iniciar a navegação (fronteiras e, quando aplicável, Floodfill), o robô usa uma **barra de bifurcacao (fork)** para executar em paralelo o **processamento do controle do sistema** e o **envio de pacotes de telemetria ao sistema web**.

3.  **Ciclo de Telemetria (Insumos e Resultados):**
    *   **Entrada:** Pacotes de telemetria transmitidos via Bluetooth/Wi-Fi.
    *   **Processamento:** O Sistema Web recebe e valida os pacotes. Caso sejam inválidos (**nó de decisão**), o pacote é descartado com a respectiva sinalização de falha de validação.

4.  **Sincronização e Atualização:** Se os dados forem válidos, o fluxo utiliza uma nova **barra de bifurcação** para atualizar simultaneamente o trajeto no mapa, os indicadores de performance e a checagem de alertas críticos (visuais e sonoros).

5.  **Pontos de Controle e Encerramento:**
    *   O sistema monitora continuamente, através de nós de decisão, se o **Objetivo foi alcançado** ou se houve um **Encerramento Manual** da sessão.
    *   **Saída Final:** Dependendo do desfecho, o status da corrida é alterado para "Desafio Cumprido" ou "Desafio Não Cumprido".
    *   A persistência automática dos dados ocorre no Banco de Dados antes de o fluxo convergir para o **estado final**.

<p style="text-align: center;">
  <em>Figura 3: Diagrama de Atividades UML</em>
</p>

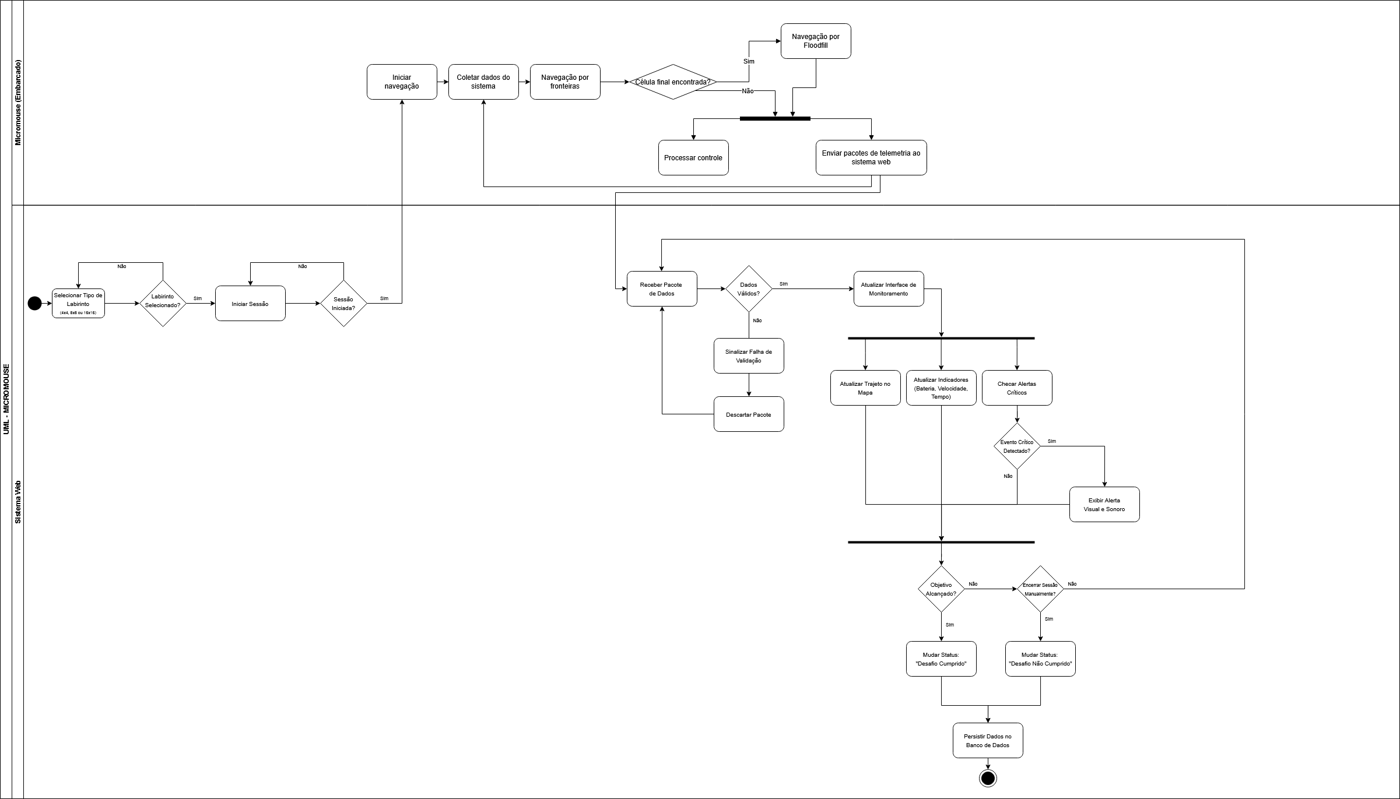
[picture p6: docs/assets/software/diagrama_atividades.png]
Diagrama de Atividades UML


<div style="text-align: center;">Autores: <a href="https://github.com/MM4k">Marcelo Makoto</a> <a href="https://github.com/dudaa28">Maria Eduarda</a></div>

---

### 6.1.1 Componentes Web

### Interface Web

Responsável por:

- monitoramento em tempo real;
- visualização do mapa;
- exibição dos indicadores da corrida;
- consulta histórica.

---

### Backend FastAPI

Responsável por:

- recebimento da telemetria;
- validação dos pacotes;
- gerenciamento das sessões;
- persistência dos dados;
- distribuição das atualizações via WebSocket.

---

### 6.1.2 Componentes Embarcados

### Subsistema de Energia

Responsável por:

- alimentação do sistema;
- monitoramento energético;
- regulação de tensão;
- cálculo de carga da bateria.

#### Componentes principais

- bateria Li-Po;
- INA226;
- regulador buck MP1584EN.

---

### Subsistema de Sensoriamento

Responsável por:

- aquisição de dados inerciais;
- medição de distância;
- detecção de obstáculos;
- apoio à navegação.

#### Componentes principais

- MPU-9250;
- 3 sensores VL53L0X.

---

### Subsistema de Atuação e Odometria

Responsável por:

- movimentação do robô;
- controle de velocidade;
- medição de deslocamento;
- controle direcional.

#### Componentes principais

- motores N20;
- encoders;
- TB6612FNG.

---

### Subsistema de Armazenamento

Responsável por:

- armazenamento local de telemetria;
- logging de execução;
- persistência de dados para análise pós-corrida.

#### Componentes principais

- módulo SD Card via SPI.

---

### Subsistema de Comunicação

Responsável por:

- envio de telemetria;
- comunicação com o backend;
- sincronização em tempo real.

#### Tecnologias utilizadas

- Wi-Fi nativa do ESP32;
- HTTP/REST;
- WebSocket.

---

### Firmware de Navegação

Responsável por:

- exploração do labirinto;
- mapeamento;
- cálculo da rota otimizada;
- controle de estados da navegação.

#### Algoritmos utilizados

- Frontier-based Exploration;
- Flood Fill;
- Path Planning.

---

### 6.2 Visão de Processos

A visão de processos descreve o comportamento dinâmico do sistema durante uma corrida.

---

### 6.2.1 Fluxo Operacional

1. O sistema aguarda a configuração da sessão.
2. O usuário seleciona o labirinto.
3. O Micromouse inicializa sensores e motores.
4. O algoritmo de navegação inicia a exploração.
5. O firmware coleta dados dos sensores.
6. A telemetria é enviada ao backend via HTTP/REST.
7. O backend valida os pacotes recebidos.
8. O frontend recebe atualizações em tempo real via WebSocket.
9. O backend persiste os dados históricos.
10. O Micromouse executa a rota otimizada.
11. A sessão é encerrada.

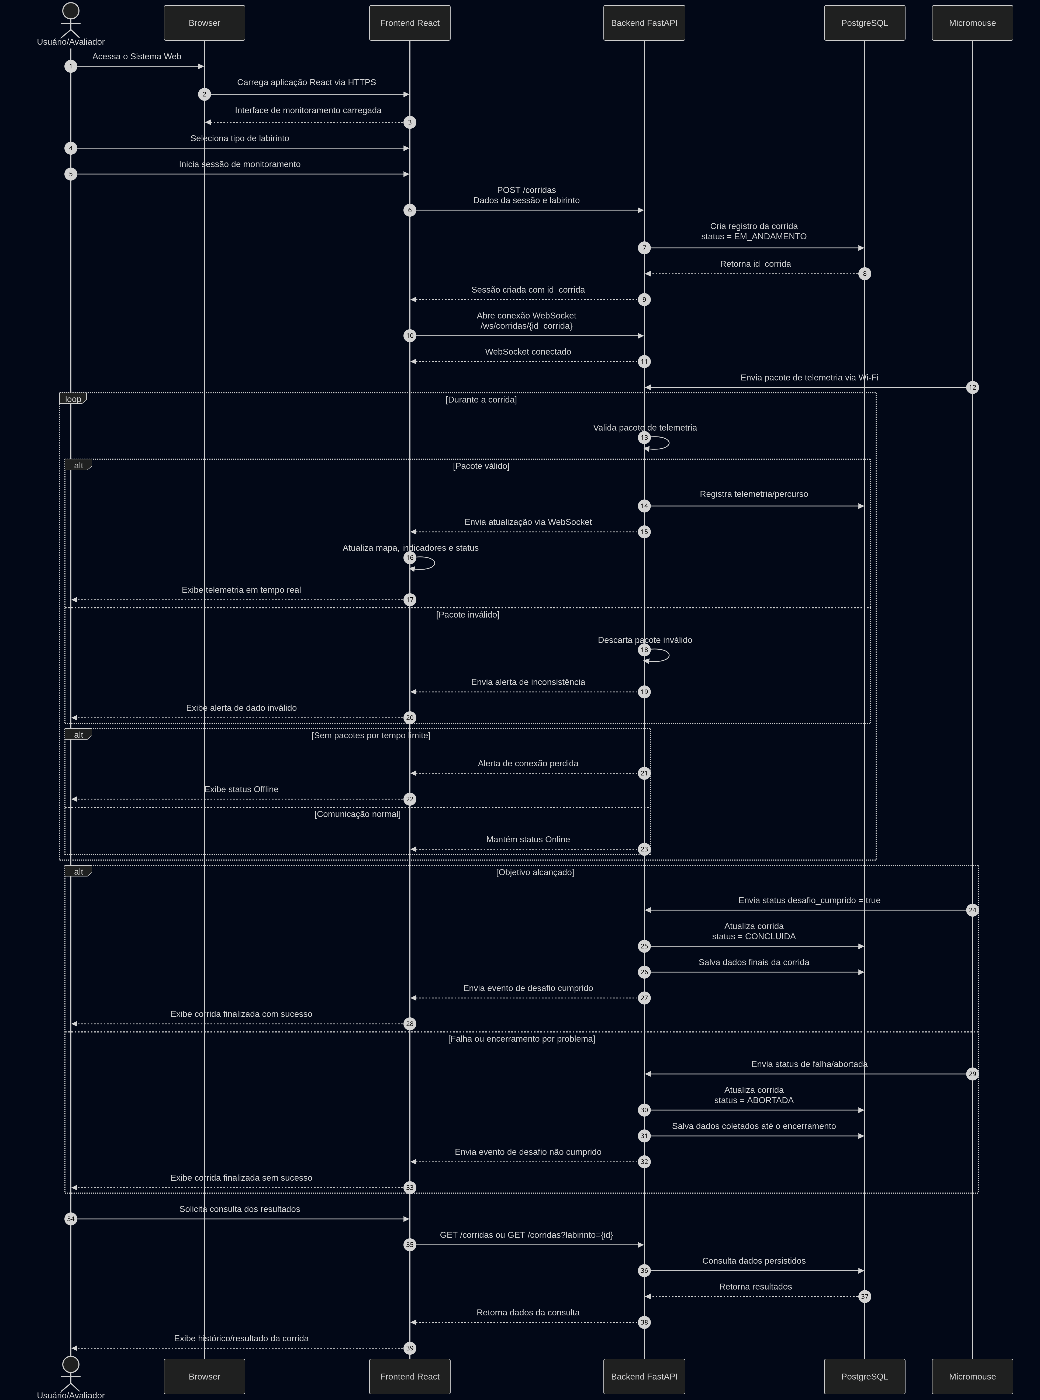
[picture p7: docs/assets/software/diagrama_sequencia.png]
Diagrama de Sequência - Ciclo de Vida da Corrida


<div style="text-align: center;">
  Autores:
  <a href="https://github.com/Potatoyz908">Euller</a> e
  <a href="https://github.com/dudaa28">Maria Eduarda</a>
</div>

### 6.2.2 Processos Embarcados

O firmware embarcado executa processos concorrentes utilizando FreeRTOS.

### Tasks principais

| Task | Intervalo | Responsabilidade |
|---|---|---|
| `battery_task` | 500 ms | Monitoramento energético |
| `imu_task` | 100 ms | Leitura da IMU |
| `tof_task` | 200 ms | Leitura dos sensores ToF |
| `motor_task` | 250 ms | Leitura de encoders |
| `data_aggregation_task` | 500 ms | Agregação de telemetria |

---

### 6.2.3 Fluxo de Telemetria

1. Sensores são lidos em tasks independentes.
2. Os dados são agregados em uma estrutura compartilhada.
3. A task de agregação monta a estrutura `RobotData`.
4. Em paralelo, a telemetria é enviada ao backend.
5. O backend valida, processa e persiste os dados.

---

### 6.2.4 Máquina de Estados da Navegação

O sistema embarcado utiliza uma máquina de estados responsável pelas transições de navegação.

### Estados principais

- IDLE;
- FRONTIER;
- FLOODFILL;
- OPTIMAL;
- DONE.

### Fluxo de estados

```text
IDLE → FRONTIER → FLOODFILL → OPTIMAL → DONE
```

---

### 6.2.5 Tratamento de Exceções

O sistema considera:

- perda de conexão;
- falha de validação;
- perda de sensores;
- baixa tensão da bateria;
- encerramento manual;
- falha da corrida.

---

### 6.3 Visão de Implementação

A visão de implementação descreve como os componentes são organizados tecnologicamente.

### 6.3.1 Estrutura de Camadas e Pacotes (Diagrama de Pacotes)

O diagrama a seguir apresenta a organização do sistema em camadas (Apresentação, Aplicação e Dados) e os respectivos pacotes/módulos que compõem cada uma delas, detalhando a estrutura lógica descrita acima.

<p style="text-align: center;">
  <em>Figura: Diagrama de Pacotes</em>
</p>

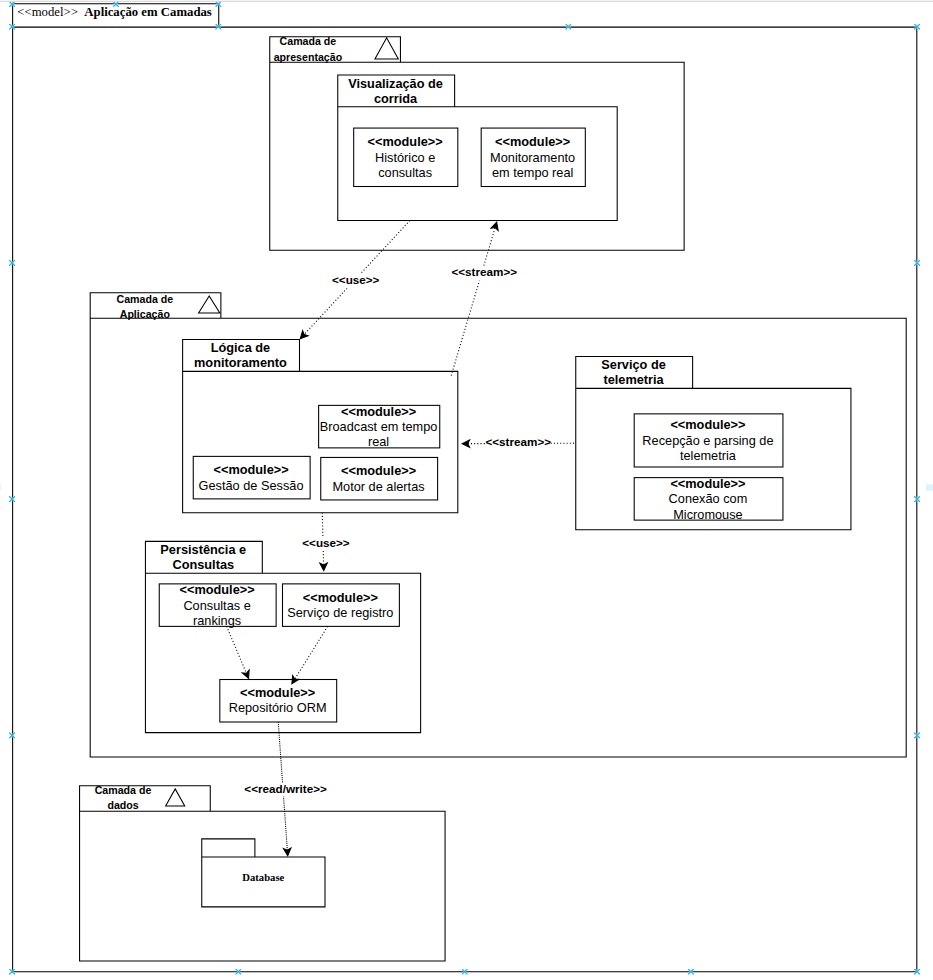
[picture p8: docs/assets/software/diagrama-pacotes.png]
Diagrama de Pacotes


<div style="text-align: center;">Autor: <a href="https://github.com/GabrielCastelo-31">Gabriel Castelo</a></div>

### 6.3.1 Frontend

O frontend React é organizado em:

- **Computador do Usuário:** executa o navegador;
- **Servidor Frontend:** disponibiliza a aplicação React;
- **Servidor Backend:** executa a aplicação FastAPI;
- **Fonte de Telemetria:** representa o Micromouse;
- **Servidor de Banco de Dados:** executa o PostgreSQL.

A comunicação entre os nós ocorre por meio dos seguintes protocolos:

- **HTTPS:** comunicação entre navegador e frontend;
- **HTTPS/REST:** comunicação tradicional entre frontend e backend;
- **WSS/WebSocket:** comunicação em tempo real entre frontend e backend;
- **Wi-Fi:** envio de telemetria do Micromouse ao backend;
- **TCP/IP:** comunicação entre backend e banco de dados.

#### Diagrama de Implantação

O diagrama de implantação apresenta uma visão física e tecnológica da solução. Ele mostra onde cada parte do sistema será executada e como os componentes se comunicam.

A arquitetura proposta considera que o usuário acessa o sistema por meio de um navegador. A interface web é desenvolvida em React e se comunica com o backend desenvolvido em FastAPI. O backend recebe os dados do Micromouse, processa a telemetria, envia atualizações em tempo real para o frontend via WebSocket e persiste os dados no PostgreSQL.

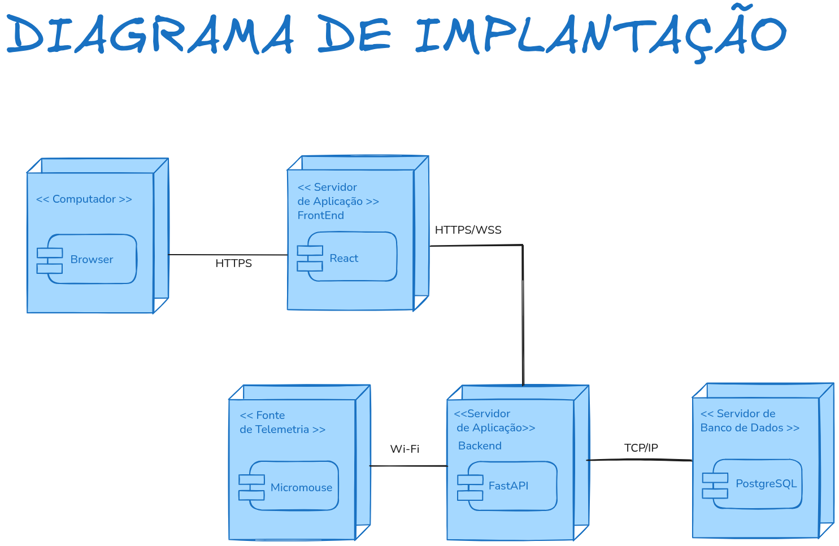
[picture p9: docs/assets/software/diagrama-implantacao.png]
Diagrama de Implantação


<div style="text-align: center;">Autor: <a href="https://github.com/Potatoyz908">Euller</a></div>

---

### 6.3.2 Backend

O backend FastAPI é organizado em:

- API REST;
- gerenciamento de WebSocket;
- serviços de telemetria;
- serviços de persistência;
- modelos de dados.

Como a solução utiliza um banco de dados relacional, foi utilizado um **Modelo Entidade-Relacionamento (MER)** e seu respectivo **Diagrama Entidade-Relacionamento (DER)**, além do diagrama lógico de dados(DLD).

#### 6.5.1 Modelo Entidade-Relacionamento (MER)

**IDENTIFICAÇÃO DAS ENTIDADES**

- **LABIRINTO**
- **CELULA**
- **CORRIDA**
- **TELEMETRIA**

**DESCRIÇÃO DAS ENTIDADES (ATRIBUTOS)**

- **LABIRINTO** (**id_labirinto**, tipo_labirinto)
- **CELULA** (**id_celula**, coordenada_x, coordenada_y, parede_norte, parede_sul, parede_leste, parede_oeste, id_labirinto)
- **CORRIDA** (**id_corrida**, desafio_cumprido, status_corrida, data_hora_inicio, data_hora_fim, id_labirinto)
- **TELEMETRIA** (velocidade_media, tempo_total, tensao_media, corrente_media, velocidade_maxima_percurso, id_corrida)

#### 6.5.2 Diagrama Entidade-Relacionamento (DER)

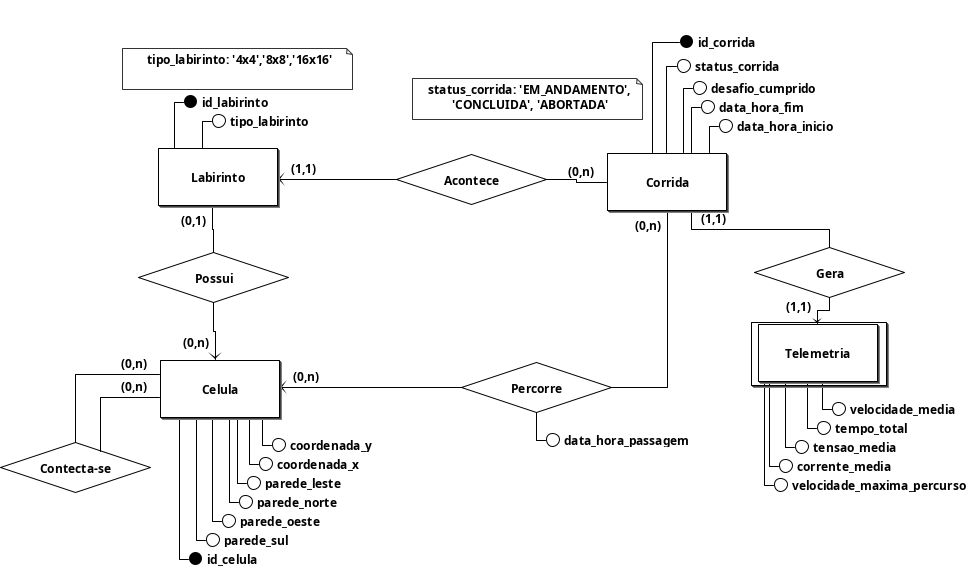
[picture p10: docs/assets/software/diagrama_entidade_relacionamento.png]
Diagrama Entidade-Relacionamento


<div style="text-align: center;">Autores: <a href="https://github.com/GabrielCastelo-31">Gabriel Castelo</a> e <a href="https://github.com/mtsmgn0">Mateus Magno</a></div>

#### 6.5.3 Diagrama Lógico de Dados (DLD)

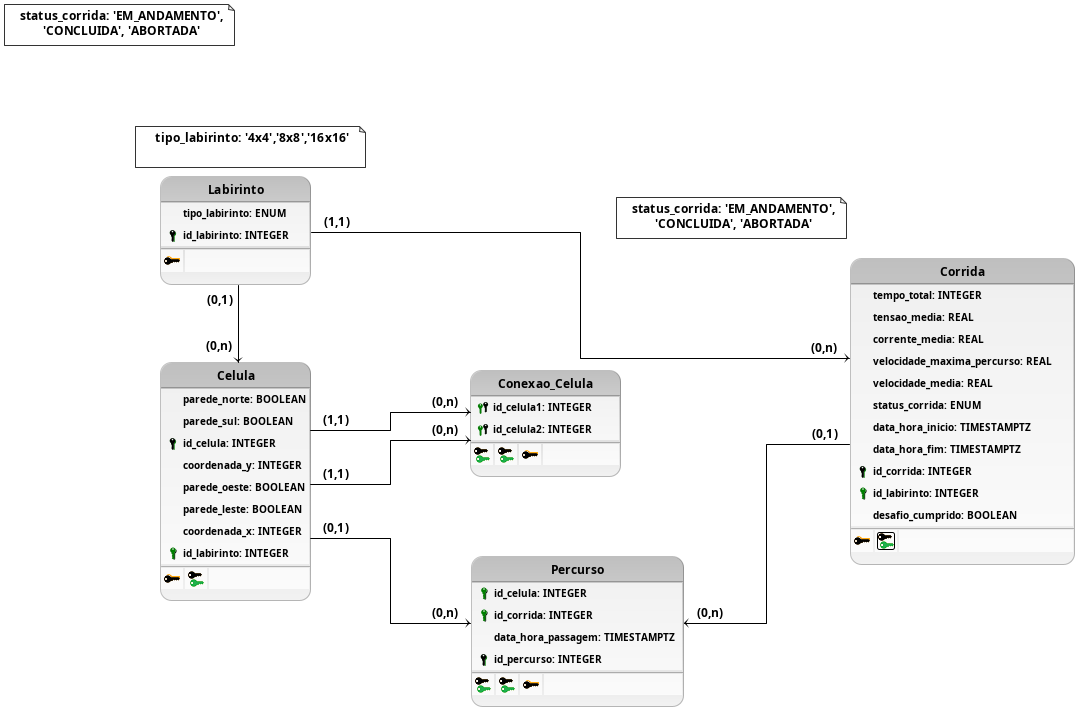
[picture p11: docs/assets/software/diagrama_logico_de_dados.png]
Diagrama Lógico de Dados


<div style="text-align: center;">Autor: <a href="https://github.com/GabrielCastelo-31">Gabriel Castelo</a></div>

---

### 6.3.3 Organização do Firmware

O firmware embarcado é desenvolvido utilizando:

- ESP32;
- ESP-IDF;
- FreeRTOS;
- linguagem C/C++.

---

### Estrutura de Arquivos

```text
main/
├── app/main.cpp
├── i2c_manager.{cpp,hpp}
├── pins.hpp
├── battery/
├── imu/
├── motor/
├── vl53l0x/
└── sd_card/
```

---

### Módulos principais

| Módulo | Responsabilidade |
|---|---|
| `battery` | Monitoramento energético |
| `imu` | Interface da IMU |
| `motor` | Controle dos motores |
| `vl53l0x` | Sensoriamento ToF |
| `sd_card` | Persistência local |
| `i2c_manager` | Gerenciamento I2C |

---

### 6.3.4 Hardware Integrado

| Componente | Responsabilidade |
|---|---|
| ESP32 | Processamento principal |
| INA226 | Monitoramento energético |
| MP1584EN | Regulação de tensão |
| VL53L0X | Sensoriamento de distância |
| MPU-9250 | Medição inercial |
| TB6612FNG | Controle dos motores |
| Encoders | Odometria |
| SD Card | Armazenamento local |

---

### 6.3.5 Barramento I2C Compartilhado

### Configuração

| Sinal | GPIO |
|---|---|
| SDA | GPIO_NUM_21 |
| SCL | GPIO_NUM_22 |

### Dispositivos conectados

- INA226;
- MPU-9250;
- sensores VL53L0X.

### Características

- clock de 100 kHz;
- gerenciamento centralizado via `i2c_manager`;
- compartilhamento de barramento entre sensores.

# 6.4 Visão de Implantação

A visão de implantação apresenta os nós físicos da solução.

## 6.4.1 Nós de Execução

| Nó | Responsabilidade |
|---|---|
| Micromouse | Execução do firmware |
| Navegador do Usuário | Interface web |
| Servidor Backend | API FastAPI |
| Servidor PostgreSQL | Persistência dos dados |

---

## 6.4.2 Comunicação

| Origem | Destino | Protocolo |
|---|---|---|
| Micromouse | Backend | HTTP/REST via Wi-Fi |
| Backend | Frontend | WebSocket (WSS) |
| Frontend | Backend | HTTPS |
| Backend | PostgreSQL | TCP/IP |

---

## 6.4.3 Implantação do Sistema Embarcado

O firmware é executado diretamente no ESP32 embarcado no Micromouse.

### Interfaces utilizadas

- I2C;
- SPI;
- GPIO;
- PWM;
- UART.

---

## 6.4.4 Implantação Física dos Sensores

| Subsistema | Interface |
|---|---|
| MPU-9250 | I2C |
| INA226 | I2C |
| VL53L0X | I2C |
| SD Card | SPI |
| Motores | PWM/GPIO |
| Encoders | GPIO/PCNT |

---

## 6.4.5 Ambiente de Implantação

Durante o desenvolvimento acadêmico, os serviços podem ser executados em rede local.

A solução também permite futura implantação utilizando containers Docker ou infraestrutura em nuvem.

---

# 6.5 Visão de Dados

A visão de dados descreve como as informações são persistidas.

O modelo utiliza PostgreSQL e segue uma estrutura relacional.

---

## 6.5.1 Entidades Principais

### LABIRINTO

- id_labirinto
- dimensao

---

### CELULA

- id_celula
- coordenada_x
- coordenada_y
- parede_norte
- parede_sul
- parede_leste
- parede_oeste
- id_labirinto

---

### CORRIDA

- id_corrida
- data_inicio
- data_fim
- desafio_cumprido
- finalizada
- id_labirinto

---

### TELEMETRIA

- id_telemetria
- timestamp
- velocidade_media
- velocidade_maxima
- tensao
- corrente
- posicao_x
- posicao_y
- temperatura
- id_corrida

---

### EVENTO

- id_evento
- timestamp
- tipo_evento
- descricao
- id_corrida

---

## 6.5.2 Relacionamentos

- um labirinto possui várias células;
- um labirinto pode possuir várias corridas;
- uma corrida possui vários registros de telemetria;
- uma corrida possui vários eventos.

---

# 7. Segurança

Mesmo sendo um projeto acadêmico, a arquitetura considera mecanismos básicos de segurança.

## Medidas previstas

- utilização de HTTPS/WSS;
- validação dos pacotes recebidos;
- descarte de mensagens inválidas;
- controle de sessão;
- separação entre frontend e backend.

---

# 8. Relação com os Requisitos

| Requisito | Atendimento |
|---|---|
| Receber dados do Micromouse | Backend FastAPI |
| Exibir telemetria em tempo real | WebSocket + React |
| Persistir dados históricos | PostgreSQL |
| Validar telemetria | Backend FastAPI |
| Consultar corridas | API REST |
| Exibir indicadores da corrida | Frontend React |
| Monitorar bateria | INA226 + Backend |
| Registrar logs locais | SD Card |
| Executar navegação autônoma | Firmware ESP32 |

---

# 9. Considerações Finais

A arquitetura proposta busca equilibrar simplicidade, organização e capacidade de expansão.

A separação entre frontend, backend, persistência e firmware facilita o desenvolvimento em equipe e permite evolução futura da solução.

O uso de WebSocket atende aos requisitos de monitoramento em tempo real, enquanto o PostgreSQL fornece armazenamento estruturado para consultas históricas.

No sistema embarcado, a utilização de FreeRTOS, ESP-IDF e organização modular do firmware permite concorrência entre sensores, controle e comunicação, facilitando manutenção e expansibilidade.

---

## 10. Histórico de Versões

|Versão|Data|Autor|Descrição|Revisor |
|---|---|---|---|---|
|1.0|03/05/2026|[Euller](https://github.com/Potatoyz908)|Criação do documento|[Gabriel Castelo](https://github.com/GabrielCastelo-31)|
|1.1|04/05/2026|[Euller](https://github.com/Potatoyz908)|Atualização dos diagramas e adição de mais informações|[Gabriel Castelo](https://github.com/GabrielCastelo-31)|
|1.2 | 04/05/2026|[Gabriel Castelo](https://github.com/GabrielCastelo-31) | Revisão do documento e adição do histórico de versão| [Maria Eduarda](https://github.com/dudaa28)
|1.3 | 04/05/2026|[Gabriel Castelo](https://github.com/GabrielCastelo-31) | Adição do MER e DER|[Maria Eduarda](https://github.com/dudaa28)
|1.4 | 04/05/2026|[Maria Eduarda](https://github.com/dudaa28) | Adição do diagrama de atividades UML| - |
|1.4.1 | 04/05/2026|[Maria Eduarda](https://github.com/dudaa28) | Adição do diagrama de atividades UML| [Gabriel Castelo](https://github.com/GabrielCastelo-31)|
|1.4.2 | 05/05/2026|[Euller Júlio](https://github.com/Potatoyz908) | Correção no diagrama de implantação UML| [Gabriel Castelo](https://github.com/GabrielCastelo-31)|
|1.5 | 05/05/2026|[Gabriel Castelo](https://github.com/GabrielCastelo-31) | Adição do diagrama lógico de dados| [Euller Júlio](https://github.com/Potatoyz908)|
|1.5.1 | 05/05/2026|[Euller Júlio](https://github.com/Potatoyz908) | Correção no diagrama de implantação UML| [Maria Eduarda](https://github.com/dudaa28) |
|1.6 | 08/05/2026|[Gabriel Castelo](https://github.com/GabrielCastelo-31) | Adição do diagrama de pacotes| [Euller Júlio](https://github.com/Potatoyz908)
|1.7 | 09/05/2026|[Maria Eduarda](https://github.com/dudaa28) | Adição do Diagrama  de Sequências e Atualização da página| [Euller Júlio](https://github.com/Potatoyz908) |
|1.8 | 09/05/2026|[Euller Júlio](https://github.com/Potatoyz908) | Adição de diagramas de sequência e explicação da arquitetura adotada| [Victor Pontual](https://github.com/VictorPontual)|
|2.0 | 10/05/2026 | [Victor Pontual](https://github.com/VictorPontual) | Revisão estrutural da arquitetura e integração completa das visões de hardware e software embarcado | - |

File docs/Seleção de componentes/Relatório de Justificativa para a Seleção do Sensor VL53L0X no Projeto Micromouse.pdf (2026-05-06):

Relatório de Justificativa para a Seleção do Sensor VL53L0X no Projeto Micromouse

Introdução

Este relatório apresenta a justificativa técnica para a escolha do sensor de tempo de voo (Time-of-Flight – ToF) VL53L0X como principal dispositivo de medição de distância no projeto Micromouse. A decisão foi baseada em critérios como precisão, dimensões físicas, velocidade de aquisição e desempenho em ambientes internos controlados e valor.

Inicialmente, será utilizada uma configuração com quatro sensores distribuídos ao redor do robô. Considerando o campo de visão (Field of View – FoV) aproximado de 25° de cada sensor, essa configuração proporciona uma cobertura adequada para detecção de paredes e alinhamento durante a navegação no labirinto.

Justificativa da Escolha do VL53L0X

O sensor VL53L0X, desenvolvido pela STMicroelectronics, foi selecionado por oferecer um conjunto de características altamente compatíveis com os requisitos de um robô Micromouse.

### 1. Princípio de Medição (Time-of-Flight – ToF)

Diferentemente de sensores ultrassônicos e sensores infravermelhos baseados em triangulação, o VL53L0X utiliza o tempo de voo de um feixe de laser infravermelho para determinar a distância até o objeto.

Esse princípio oferece vantagens importantes:

- Alta precisão: medições com resolução na ordem de milímetros, com menor dependência da cor e refletividade da superfície.
- Baixa variabilidade: maior consistência em superfícies comuns de labirintos (paredes claras, escuras ou texturizadas).
- Alta taxa de atualização: medições rápidas, adequadas para robôs em movimento contínuo e em alta velocidade.

### 2. Dimensões e Integração

O VL53L0X possui dimensões extremamente reduzidas, permitindo fácil integração ao chassi do Micromouse sem impacto significativo no volume ou no centro de massa do robô.

Essa característica é especialmente relevante em projetos Micromouse, onde o espaço físico é limitado e a distribuição de peso influencia diretamente na estabilidade e desempenho dinâmico.

### 3. Alcance e Adequação ao Ambiente

O sensor apresenta alcance nominal de até aproximadamente 2 metros, porém com melhor desempenho em distâncias menores — exatamente a faixa de operação típica do Micromouse (inferior a 30 cm).

Além disso:

- O feixe estreito permite detecção direcional mais precisa.
- Há menor suscetibilidade a interferência luminosa ambiente em comparação com sensores IR convencionais.
- Reduz-se o risco de leituras cruzadas entre sensores adjacentes.

### 4. Interface e Integração Eletrônica

O VL53L0X utiliza comunicação via protocolo I²C, o que simplifica significativamente a integração com microcontroladores como ESP32, comum em projetos embarcados.

Isso permite:

- Redução no número de pinos utilizados.
- Facilidade na leitura simultânea de múltiplos sensores (com controle de endereçamento).
- Integração direta com bibliotecas já disponíveis.

Comparação com Tecnologias Alternativas
Característica | VL53L0X (ToF) | Sensores IR Analógicos | Sensores Ultrassônicos
Princípio | Tempo de voo (laser) | Triangulação IR | Tempo de voo (som)
Precisão | Alta (mm) | Média (dependente da superfície) | Baixa (cm)
Campo de visão | Estreito | Estreito/Médio | Largo (cone)
Velocidade | Alta | Média | Baixa
Interface | I²C | Analógica | Digital
Suscetibilidade a ruído | Baixa | Alta | Média/Alta
Tamanho | Muito compacto | Médio | Grande

Considerações de Projeto

Apesar das vantagens, alguns pontos devem ser considerados:

- Sensores ToF podem apresentar degradação de desempenho em superfícies altamente absorventes ou em ângulos muito inclinados.
- É necessário gerenciar corretamente os endereços I²C ao utilizar múltiplos sensores (uso do pino XSHUT).
- A calibração e filtragem de dados podem ser necessárias para maior estabilidade.

Conclusão

A escolha do VL53L0X é plenamente justificada pela necessidade de medições rápidas, precisas e confiáveis em curtas distâncias. Seu princípio de funcionamento baseado em tempo de voo, aliado ao tamanho compacto e à interface digital, torna-o altamente adequado para aplicações em robôs Micromouse.

Essas características contribuem diretamente para uma navegação mais eficiente, melhor alinhamento com as paredes e maior robustez na construção do mapa do labirinto.

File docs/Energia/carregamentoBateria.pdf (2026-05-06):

# Sistemas de Carregamento

A escolha entre baterias recarregáveis e descartáveis para o desenvolvimento de um robô que resolve labirintos é um fator importante para a viabilidade técnica do projeto. As recarregáveis de Li-ion 18650 mostram-se superiores por possuírem alta densidade energética, o que permite atingir maior autonomia com eficiência. Diferente das descartáveis, que sofrem quedas graduais de voltagem, as baterias de lítio mantêm uma tensão estável, garantindo que os motores preservem o torque e os sensores operem com precisão constante.

Embora pilhas descartáveis apresentem menor custo inicial, o sistema não suporta os picos de corrente exigidos pela movimentação, o que frequentemente causa reinicializações no microcontrolador.

Para carregar baterias de Li-ion e especificamente as células do formato 18650 existem algumas abordagens principais:

## 1. Carregadores Externos (Slot)

Esta é a opção mais segura e prática para quem utiliza pilhas individuais, como a Pilha GREEN 18650.

- Funcionamento: Remove-se as pilhas do compartimento do robô e as coloca em um carregador de tomada dedicado.
- Vantagens: Possuem circuitos de proteção internos que controlam a corrente e a tensão automaticamente, desligando ao atingir a carga total.

## 2. Módulos de Carga TP4056 (Carga via USB)

É possível carregar as baterias sem removê-las do robô, este módulo é uma boa opção para prototipagem com células 18650 de 3.7V.

- Funcionamento: Um pequeno chip que recebe energia de uma porta Micro-USB ou USB-C e gerencia a carga da bateria.
- Integração: Pode ser colado ou parafusado na estrutura do "rato" robótico.

Comparativo de Usabilidade

Opção | Melhor para... | Facilidade

Carregador de Slot | Pilhas individuais (ex: GREEN 18650) | Alta (Plug & Play)
Módulo TP4056 | Carregamento interno via USB (Praticidade no campo) | Média (Exige solda)

Comparativo de Custo-Benefício e Segurança

Critério | Carregador Externo (Slot) | Módulo TP4056 (Com Proteção)
Custo Inicial | Maior. Um carregador confiável custa entre R$ 40 e R$ 100. | Muito Baixo. Cada módulo custa entre R$ 5 e R$ 10.
Segurança | Alta. Possui circuitos dedicados e carcaça isolante profissional. | Média. Depende da qualidade da soldagem e do isolamento no robô.
Praticidade | Baixa. Exige remover as pilhas do robô toda vez que for carregar. | Alta. Permite carregar via USB (como um celular) sem abrir o robô.
Proteção no Uso | Nenhuma. Ele só protege durante a carga, não enquanto o robô corre. | Completa. Protege contra descarga excessiva e curto-circuito durante a operação.
Escalabilidade | Limitado ao número de slots físicos do aparelho. | Pode ser integrado individualmente para cada pack de bateria.

## 3. Exemplos para Aquisição

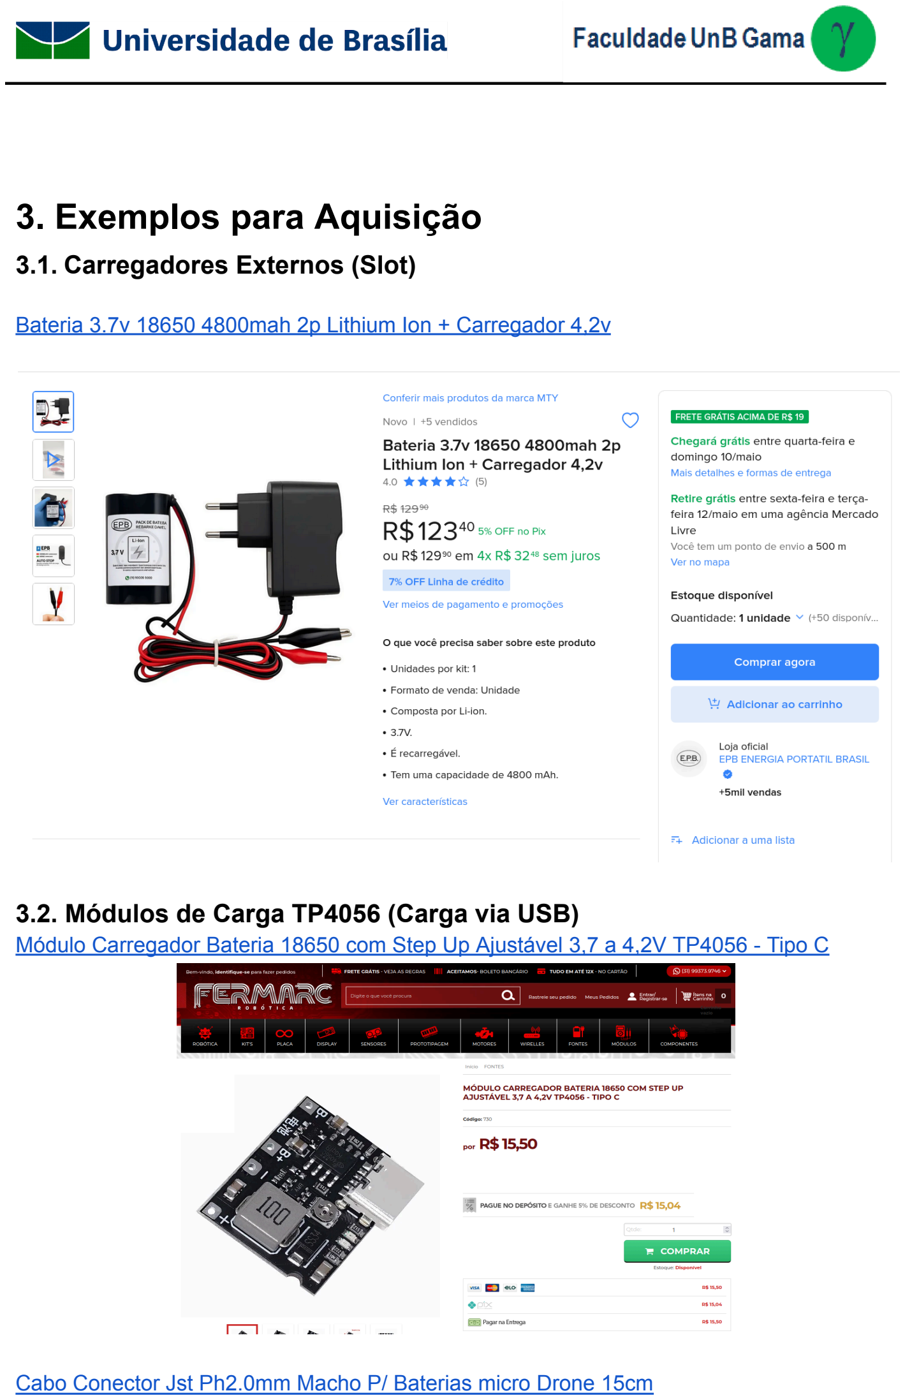
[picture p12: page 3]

### 3.1. Carregadores Externos (Slot)

Bateria 3.7v 18650 4800mah 2p Lithium Ion + Carregador 4,2v (https://www.mercadolivre.com.br/bateria-37v-18650-4800mah-2p-lithium-ion---carregador-42v/up/MLBU1404615007)

### 3.2. Módulos de Carga TP4056 (Carga via USB)

Módulo Carregador Bateria 18650 com Step Up Ajustável 3,7 a 4,2V TP4056 - Tipo C (https://www.fermarc.com/m-dulo-carregador-bateria-18650-com-step-up-ajust-vel-3-7-a-4-2v-tp4056)

Cabo Conector Jst Ph2.0mm Macho P/ Baterias micro Drone 15cm (https://shopee.com.br/product/313771325/22897898149?gad_source=1&gad_campaignid=21445281076)

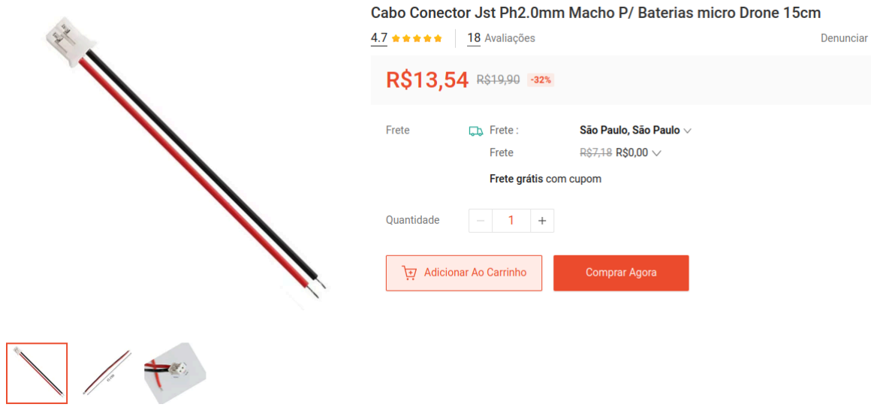
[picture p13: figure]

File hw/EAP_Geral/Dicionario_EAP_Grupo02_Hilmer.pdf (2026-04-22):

UNIVERSIDADE DE BRASÍLIA - UNB FACULDADE DE CIÊNCIAS E TECNOLOGIAS EM ENGENHARIA - FCTE PROJETO INTEGRADOR DE ENGENHARIA 1

Arthur Pinheiro Marinho - 231011112; Caio Venâncio do Rosário - 231027195; Cristiano Borges de Morais - 222033952; Eduardo de Pina Moreira Santos - 231034494; Enzo Emir Viana Ferraz - 231011293; Euller Júlio da Silva - 231026714;
Gabriel Henrique Castelo Costa - 221008051; Geovana Almeida Miranda Sant'Ana - 231027088; Giovanna Aguiar de Brito - 241011090; Giovanni Mateus de Mendonça Leles - 231027097; João Maurício Pilla Nascimento - 231011533; Marcelo Makoto Araki Takechi - 231026465; Maria Eduarda Quaresma de Andrade - 222037577; Matheus Eiki Kimura Rezende - 241025327; Mateus Magno Ferreira Soares - 222021998; Pablo Serra Carvalho - 221008679; Rafael Oliveira Montagner Melatti - 241011626; Tiago Antunes Balieiro - 231011838; Victor Pontual Guedes Arruda Nóbrega - 211029601; Vitor Gonçalves de Andrade - 261025182.

Estrutura Analítica do Projeto (EAP): “Competição Micromouse - carrinho que resolve labirintos”

Professor: Hilmer Rodrigues Neri

Gama, Brasília - DF
Abril de 2026

SUMÁRIO

### 1. OBJETIVO GERAL

Desenvolver um Micromouse (robô autônomo resolvedor de labirintos) e um labirinto de teste, atendendo aos requisitos do projeto e realizando as entregas nos checkpoints estabelecidos. O Micromouse deverá alcançar as salas retangulares centrais de três labirintos desconhecidos, organizados da seguinte forma:

a) 1º labirinto: 4x4 células, 72 cm de lado;
b) 2º labirinto: 8x8 células, 144 cm de lado;
c) 3º labirinto: 4x4 células, 288 cm de lado.

### 2. OBJETIVOS ESPECÍFICOS (REQUISITOS)

### 2.1 Requisitos do Labirinto

Para que o Micromouse possa desvendar os labirintos conforme o objetivo do produto, a equipe deverá construir uma estrutura que atenda aos seguintes requisitos:

a) Cada célula dos três labirintos possui 18 cm de lado.
b) As paredes têm 5 cm de altura e 1,2 cm de espessura.
c) As paredes são brancas com topos vermelhos.
d) O chão é preto.
e) A equipe deverá desenvolver uma pista 4x4 simplificada de testes, com condições análogas às da competição.

### 2.2 Requisitos do Micromouse

O robô deverá operar de forma totalmente autônoma, sem qualquer intervenção humana durante a resolução. Para tanto, deve atender aos seguintes requisitos:

a) Resolver cada labirinto monitorando sua localização, descobrindo paredes, mapeando o trajeto e detectando quando alcança o objetivo.
b) Não exceder 25 cm de comprimento ou largura, não havendo restrição de altura.
c) Não são permitidos voo, salto, escalada ou propulsão por combustão ou foguete.
d) O Micromouse poderá ser desqualificado caso cause danos ao labirinto.
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

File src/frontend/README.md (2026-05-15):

# Frontend do Projeto

Este diretório contém a aplicação web do projeto, construída com React + TypeScript, empacotada com Vite e estilizada com Tailwind CSS.

## Pré-requisitos

- Node.js 20 ou superior
- npm 10 ou superior

## Como rodar em desenvolvimento

1. Abra o terminal na raiz do repositório.
2. Entre na pasta do frontend:

```bash
cd src/frontend
```

3. Instale as dependências:

```bash
npm install
```

4. Inicie o servidor de desenvolvimento:

```bash
npm run dev
```
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

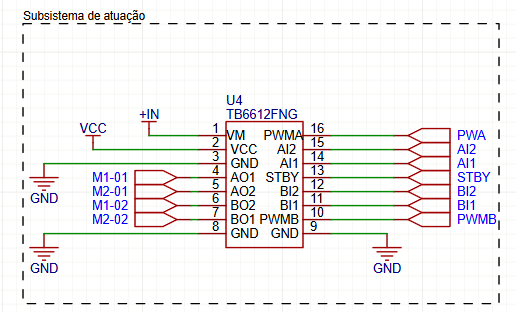
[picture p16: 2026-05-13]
hw/PCB/Esquematicos/esquematico-Subsistema de atuação.png

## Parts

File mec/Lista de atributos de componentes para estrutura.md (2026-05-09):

# Lista de atributos de componentes

Este documento foi criado pela equipe de estrutura para ter uma referência mais precisa para os componentes a serem
utilizados no robô, com intermédio da equipe de eletrônica.

## Tabela de atributos dos Componentes

| Componente | Qtde | Peso (g) | Tamanho (CxLxA) |
|---|---|---|---|
| Microcontrolador ESP32 | 1 | 9g | 51 x 27,5 x 5 mm | 
| Sensor VL53L0X | 6 | 1,5g | 25 × 12,7 × 3,5mm |
| Motor N20 (6V) | 2 | 20g | 35 x 12 x 10 mm | 
| Driver (DRV8833/TB6612) | 1 | 1,5g | 18,5 x 16,3 x 3,2mm |
| Sensor MPU6050 | 1 | 3g | 20 x 16 x 2mm |
| SD Reader hw125 | 1 | 5g | 42 x 24 x 12mm | 
| Regulador (MP1584EN) | 1 | 5g | 22 x 17 x 4mm  | 
| Bateria | 1 | 100g | 65 x 35 x 20mm | 

Referências:
- [Referência da ESP32*](https://www.eletrogate.com/modulo-wifi-esp32s-bluetooth-38-pinos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)
- [Referência do sensor VL53L0X](https://blog.eletrogate.com/sensor-de-distancia-laser-gy-vl53l0xv2/)
- [Referência do motor N20 6V 750 RPM com encoder](https://www.robocore.net/motor-caixas-de-reducao/micro-motor-caixa-de-reducao-6v-750rpm-com-encoder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)
- [Referência Driver DRV8833](https://www.makerhero.com/produto/driver-motor-ponte-h-drv8833/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)
- [Referência do MPU6050](https://www.saravati.com.br/modulo-acelerometro-e-giroscopio-3-eixos-mpu-6050-gy-521.html)
- [Referência do SD Reader](https://www.huinfinito.com.br/modulos/1432-modulo-cartao-micro-sd.html)
- [Referência do Regulador](https://www.saravati.com.br/modulo-mini-conversor-de-tensao-dc-dc-mp1584en-step-down.html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)
- [Referência da bateria](https://www.robocore.net/baterias-fontes/pack-bateria-li-ion-7_4v-2500mah-com-bms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)

## Tabela de tipos de encaixes dos componentes

| Componente | Qtde | Tipo de enxaixe | Observação |
|---|---|---|---|
| Microcontrolador ESP32 | 1 | Espaçador de Latão (PCB) | - | 
| Sensor VL53L0X | 6 | Suporte especial | - | 
| Motor N20 (6V) | 2 | Suporte rígido | - | 
| Driver (DRV8833/TB6612) | 1 | Espaçador de Latão (PCB) | - | 
| Sensor MPU6050 | 1 | Espaçador de Latão (PCB) | - | 
| SD Reader | 1 | Espaçador de Latão (PCB) | - | 
| Regulador (MP1584EN) | 1 | Espaçador de Latão (PCB) | - | 
| Bateria | 1 | Berço no meio com velcro | - |

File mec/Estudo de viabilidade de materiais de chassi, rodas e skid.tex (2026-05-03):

\documentclass[12pt, a4paper]{article}
% Estamos usando 12 pacotes
% Estes dois é para codificação de texto
\usepackage[utf8]{inputenc}
\usepackage[T1]{fontenc}
\usepackage{geometry}
\usepackage{amsmath}
\usepackage{array}
\usepackage{booktabs}
\usepackage{url}
\usepackage{helvet}
\usepackage{indentfirst}

\renewcommand{\familydefault}{\sfdefault}

% Este é o comando para por margens
\geometry{top=3cm, bottom=2cm, left=3cm, right=2cm}

% Adiciona espaçamento entre linhas de 1,5 pt
\usepackage{setspace}
\setstretch{1.5}

% Para poder modificar as tabelas
\usepackage{etoolbox}
\AtBeginEnvironment{table}{\setstretch{1.0}\fontsize{10}{12}\selectfont} % ambiente em tabelas
\AtBeginEnvironment{tabular}{\setstretch{1.0}}

% Pacote para personalizar cabeçalhos e rodapés
\usepackage{fancyhdr}
\pagestyle{fancy}
\fancyhf{}
\fancyhead[R]{\thepage}
\renewcommand{\headrulewidth}{0pt}

\setlength{\parindent}{1.25cm}

\newcommand{\fonte}[1]{\vspace{0.2cm}\par\noindent\fontsize{9}{11}\selectfont Fonte: #1}

% Aqui é a capa
\title{Estudo de Viabilidade: Materiais para Chassi, Rodas e Skid \\ 
\large Micromouse - Competição de Robôs Autônomos}
\author{Geovana Almeida Miranda Sant'Ana \\ Caio Venâncio do Rosário}
\date{1 de maio de 2026}

\begin{document}

% a partir daqui tem como gerar seções e subseções no documento
\maketitle

\newpage
\setcounter{page}{2}

\subsection*{Elaboração do estudo}

O presente estudo foi realizado em uma sessão colaborativa na plataforma Discord, com duração total de 5 horas e 28 minutos. Foram responsáveis pela pesquisa, consolidação dos dados e redação final:

\begin{itemize}
    \item Geovana Almeida Miranda Sant'Ana (231027088)
    \item Caio Venâncio do Rosário (231027195)
\end{itemize}

Todo o levantamento de coeficientes de atrito, propriedades térmicas dos materiais e análise de viabilidade técnica e orçamentária foi executado pelos autores durante o período mencionado.

% Seção 1 de introdução e objetivo
\section{Introdução e Objetivo}

Este documento avalia a viabilidade de diferentes materiais poliméricos para três componentes principais de um robô \textit{Micromouse}: \textbf{chassi}, \textbf{rodas} e \textbf{skid} (patim deslizante). O estudo considera três cenários de piso: asfalto (caso extremo de alto atrito), MDF (piso real da competição) e vidro (caso hipotético de baixo atrito).

O robô foi modelado para atingir velocidade de pico de $6 \, m/s$, caracterizando um cenário de alto desempenho. Materiais aprovados neste cenário são automaticamente adequados para robôs mais lentos.

% Seção 2 de metodologia de cálculo térmico
\section{Metodologia de Cálculo Térmico}

A geração de calor por fricção foi estimada pelo modelo de potência dissipada:

\begin{equation}
P = \mu \cdot N \cdot v
\end{equation}

Onde:
\begin{itemize}
    \item $P$ = potência térmica dissipada [W]
    \item $\mu$ = coeficiente de atrito cinético [adimensional]
    \item $N$ = força normal (peso do robô) [N]
    \item $v$ = velocidade [m/s]
\end{itemize}

\textbf{Parâmetros adotados:}
\begin{itemize}
    \item Massa do robô: $m = 0,1 \, kg$ (100 gramas)
    \item Força normal: $N = m \cdot g = 0,1 \cdot 9,81 = 0,981 \, N \approx 1 \, N$
    \item Velocidade: $v = 6 \, m/s$
\end{itemize}

A Tabela \ref{tab:potencia} apresenta a potência gerada para diferentes coeficientes de atrito.
\begin{table}[h]
\centering
\caption{Potência térmica gerada por fricção a 6 m/s}
\label{tab:potencia}
\begin{tabular}{c|c}
\hline
$\mu$ & $P$ (W) \\ \hline
0,05 & 0,30 \\
0,10 & 0,60 \\
0,30 & 1,80 \\
0,50 & 3,00 \\
0,70 & 4,20 \\ \hline
\end{tabular}
\fonte{Elaboração própria (2026).}
\end{table}

\subsection*{Critério de Falha Térmica}

Um material falha quando sua superfície atinge a \textbf{Temperatura de Transição Vítrea} ($T_g$), passando do estado rígido ao borrachudo, perdendo forma e aumentando o atrito irreversivelmente. Para elastômeros (TPU), a $T_g$ não é definida, sendo mais resistentes.

% Seção 3 de análise de coeficientes de atrito por superfície
\section{Análise de Coeficientes de Atrito por Superfície}

A Tabela \ref{tab:coef_atrito} apresenta os coeficientes de atrito estimados para cada material nas três superfícies analisadas.
\begin{table}[h]
\centering
\caption{Coeficientes de atrito estimados por material e superfície}
\label{tab:coef_atrito}
\begin{tabular}{l|c|c|c}
\hline
\textbf{Material} & \textbf{Asfalto} & \textbf{MDF} & \textbf{Vidro} \\ \hline
PLA & 0,4 - 0,5 & 0,5 - 0,6 & 0,3 - 0,4 \\
PETG & 0,3 - 0,4 & 0,4 - 0,5 & 0,15 - 0,25 \\
ABS & 0,5 - 0,6 & 0,4 - 0,55 & 0,2 - 0,3 \\
ASA & 0,5 - 0,6 & 0,4 - 0,55 & 0,2 - 0,3 \\
Nylon & 0,4 - 0,5 & 0,3 - 0,45 & 0,15 - 0,25 \\
TPU & 0,6 - 0,8 & 0,5 - 0,7 & 0,5 - 0,6 \\
PTFE (fita) & 0,05 - 0,10 & 0,04 - 0,08 & 0,04 - 0,07 \\ \hline
\end{tabular}
\fonte{Elaboração própria a partir de dados estimados (2026).}
\end{table}

% Seção 4 de risco de falha térmica
\section{Risco de Falha Térmica a 6 m/s}

A Tabela \ref{tab:falha} avalia o risco de derretimento/deformação para cada material na velocidade máxima.
\begin{table}[h]
\centering
\caption{Risco de falha térmica a 6 m/s}
\label{tab:falha}
\begin{tabular}{l|c|c}
\hline
\textbf{Material} & $T_g$ (°C) & \textbf{Risco de Falha} \\ \hline
PLA & 60 - 65 & ALTO (excede $T_g$ rapidamente) \\
PETG & 75 - 85 & MODERADO-ALTO \\
ABS & 105 - 115 & MODERADO \\
ASA & 110 - 120 & MODERADO \\
Nylon & 45 - 70* & MODERADO-ALTO (*$T_g$ baixa mas tenacidade alta) \\
TPU & --- & BAIXO (elastômero, dissipa bem) \\
PTFE & $>$300 & MUITO BAIXO \\ \hline
\end{tabular}
\fonte{Elaboração própria com base em fichas técnicas (2026).}
\end{table}

% Seção 5 de aplicação por componente
\section{Aplicação por Componente}

\subsection{Chassi}

Requisitos: rigidez, resistência ao impacto, baixa deformação térmica.

\begin{table}[h]
\centering
\caption{Materiais para chassi - ordem de preferência}
\label{tab:chassi}
\begin{tabular}{l|c}
\hline
\textbf{Material} & \textbf{Desempenho} \\ \hline
ASA & Excelente (rígido, estável, fácil de imprimir) \\
ABS & Bom (similar ao ASA, porém menos estável) \\
PETG & Regular (mais flexível, pode torcer) \\
PLA & Péssimo (frágil, deforma com calor) \\
TPU & Inadequado (muito flexível) \\ \hline
\end{tabular}
\fonte{Elaboração própria (2026).}
\end{table}

\subsection{Rodas Motorizadas}

Requisitos: alto atrito para aceleração e frenagem.

\begin{table}[h]
\centering
\caption{Materiais para rodas - ordem de preferência}
\label{tab:rodas}
\begin{tabular}{l|c}
\hline
\textbf{Material} & \textbf{Desempenho} \\ \hline
TPU & Excelente (maior $\mu$, dissipa calor bem) \\
ABS/ASA & Bom (atrito médio-alto, alternativas rígidas) \\
PLA/PETG & Não recomendado (falha térmica ou baixo atrito) \\ \hline
\end{tabular}
\fonte{Elaboração própria (2026).}
\end{table}

\subsection{Skid (Patim Deslizante)}

Requisitos: mínimo atrito, alta resistência ao desgaste.

\begin{table}[h]
\centering
\caption{Materiais para skid - ordem de preferência}
\label{tab:skid}
\begin{tabular}{l|c}
\hline
\textbf{Material} & \textbf{Desempenho} \\ \hline
Fita PTFE (Teflon) & Excelente ($\mu \approx 0,05$) \\
POM (Acetal/Delrin) & Ótimo ($\mu \approx 0,13$) \\
Nylon & Regular ($\mu \approx 0,34$) \\
ASA/ABS & Péssimo ($\mu \approx 0,5$) \\ \hline
\end{tabular}
\fonte{Elaboração própria (2026).}
\end{table}

% Seção 6 de recomendação final para o projeto
\section{Recomendação Final para o Projeto}

Considerando:
\begin{itemize}
    \item Impressora disponível: Bambu Lab X1 Carbon (câmara fechada)
    \item Orçamento: R\$ 100 por pessoa (20 pessoas = R\$ 2.000 total)
    \item Desejo de usar \textbf{um único filamento} para chassi + skid
    \item Rodas adquiridas separadamente (Lego ou comerciais)
    \item Evitar compósitos devido à anisotropia
\end{itemize}

\subsection*{Material Escolhido: ASA (Acrilonitrila Estireno Acrilato)}

\begin{table}[h]
\centering
\caption{Justificativa para escolha do ASA}
\label{tab:justificativa}
\begin{tabular}{l|l}
\hline
\textbf{Critério} & \textbf{Avaliação} \\ \hline
Custo (1kg) & R\$ 120 - 150 \\
Chassi & Excelente (rígido, resistente ao calor) \\
Skid (puro) & Ruim (alto atrito) \\
Skid + fita PTFE & Excelente (solução híbrida) \\
Impressão na X1 Carbon & Ideal (câmara fechada) \\
Anisotropia & Baixa (diferente de compósitos) \\ \hline
\end{tabular}
\fonte{Elaboração própria (2026).}
\end{table}

\subsection*{Solução Proposta}

\begin{enumerate}
    \item Imprimir \textbf{chassi} em ASA.
    \item Imprimir \textbf{skid} em ASA.
    \item Colar \textbf{fita de PTFE} (R\$ 41,46 por 2 rolos) na superfície de contato do skid.
    \item Adquirir \textbf{rodas prontas} (Lego ou rodízios comerciais).
\end{enumerate}

% Seção 7 de Orçamento estimado
\section{Orçamento Estimado (20 pessoas)}

\begin{table}[h]
\centering
\caption{Orçamento detalhado}
\label{tab:orcamento}
\begin{tabular}{l|c}
\hline
\textbf{Item} & \textbf{Valor (R\$)} \\ \hline
2 kg de ASA (2 rolos de 1kg) & 300 \\
Fita PTFE (2 rolos) & 42 \\
Rodas/rodízios (opção econômica) & $\sim$ 50 \\
\textbf{Total} & $\sim$ 392 \\ \hline
\end{tabular}
\fonte{Elaboração própria com base em cotações (2026).}
\end{table}

\textit{Obs: Orçamento muito abaixo do limite de R\$100/pessoa, permitindo folga para componentes eletrônicos.}

% Seção 8 de Conclusão
\section{Conclusão}

A combinação \textbf{ASA + fita PTFE} atende a todos os requisitos:
\begin{itemize}
    \item Chassi rígido e resistente termicamente.
    \item Skid de baixíssimo atrito com a fita.
    \item Custo acessível para o grupo.
    \item Aproveitamento máximo da impressora Bambu Lab X1 Carbon.
\end{itemize}

Alternativa secundária: \textbf{ABS} (mais barato, porém menos estável dimensionalmente) ou \textbf{PETG} (mais fácil de imprimir, porém chassi menos rígido).

\newpage

\begin{thebibliography}{99}

\bibitem{CALLISTER} CALLISTER, W. D.; RETHWISCH, D. G. \textit{Materials Science and Engineering: An Introduction}. 10. ed. Hoboken: Wiley, 2018.

\bibitem{MATWEB} MATWEB. \textit{Propriedades de materiais poliméricos}. Disponível em: \url{www.matweb.com}. Acesso em: 30 abr. 2026.

\bibitem{3DLAB} 3D LAB. \textit{Fichas técnicas de filamentos ASA, ABS, PETG, PLA, TPU, Nylon}. Disponível em: \url{www.3dlab.com.br}. Acesso em: 30 abr. 2026.

\bibitem{BAMBU} BAMBU LAB. \textit{Especificações da impressora X1 Carbon}. Disponível em: \url{www.bambulab.com}. Acesso em: 30 abr. 2026.

\bibitem{IEEE} IEEE ROBOTICS AND AUTOMATION SOCIETY. \textit{IEEE Micromouse Competition: Rules and Guidelines}. Nova York: IEEE, 2023.

\end{thebibliography}

\newpage

% Seção de Anexo A para compra de componentes a parte
\section*{ANEXO A — Levantamento de Componentes para Skid, Esferas e Rodízios}

Como parte do estudo de viabilidade, foram levantadas opções tanto para \textbf{manufatura própria (impressão 3D)} quanto para \textbf{aquisição comercial} de componentes de baixo atrito ou rolamento. Os preços foram cotados em dólares (US\$) ou reais (R\$) conforme a origem.

\subsection*{Opções para impressão própria (Thingiverse)}

\begin{itemize}
    \item \textbf{Suporte para esfera / caster caseiro} – arquivo com geometria para alojar esfera de rolamento.  
    \url{https://www.thingiverse.com/thing:8959}

    \item \textbf{Skid fixo com base para fixação} – modelo simples de patim deslizante para impressão em ABS/ASA ou nylon.  
    \url{https://www.thingiverse.com/thing:3145120}
\end{itemize}

Ambos os projetos podem ser impressos com o filamento ASA escolhido e, se necessário, receber a fita de PTFE na superfície de contato.

\subsection*{Componentes comerciais avaliados}

\subsubsection*{Rodízios adesivos (mini casters)}

\begin{itemize}
    \item \textbf{VXB – 1/2" Mini Swivel Adhesive Caster Wheels (pacote com 8)}  
    Pequenos rodízios giratórios com placa autoadesiva.  
    \url{https://vxb.com/products/1-2in-mini-swivel-adhesive-caster-wheels-8pack}

    \item \textbf{GNYOHUA – Self-Adhesive Casters (Amazon EUA)}  
    Modelo similar, com 8 peças, aplicação leve.  
    \url{https://www.amazon.com/GNYOHUA-Adhesive-Furniture-Appliances-Light-Duty/dp/B0CXPQSC9R}  
    \textbf{Preço:} US\$ 9,99 + frete de importação.
\end{itemize}

\subsubsection*{Múltiplas esferas ou esfera única}

\begin{itemize}
    \item \textbf{Esfera única para móvel (transferidor universal)} – pode ser adaptada como ponto de contato de baixo atrito.  
    \url{https://www.amazon.com/Appliance-Universal-Transfers-Furniture-Appliances/dp/B0D8PHFKRQ}  
    \textbf{Preço:} US\$ 8,49.
\end{itemize}

\subsubsection*{Fita de PTFE (baixíssimo atrito)}

\begin{itemize}
    \item \textbf{Fita deslizante para gaveta – 1,5 cm x 10 m (2 rolos)}  
    Material: PTFE, resistente à abrasão e ao calor. Disponível na Amazon Brasil.  
    \textbf{Preço:} R\$ 41,46 (2 rolos).
\end{itemize}

\subsection*{Análise de custo-benefício}

\begin{table}[h]
\centering
\caption{Comparativo entre soluções para baixo atrito}
\label{tab:comp_solucoes}
\begin{tabular}{l|c|c|c}
\hline
\textbf{Solução} & \textbf{Atrito estimado} & \textbf{Custo (R\$)} & \textbf{Observação} \\ \hline
Fita PTFE + skid impresso & Muito baixo ($\mu \approx 0,05$) & 20-30 & Mais flexível e barato \\
Caster adesivo (8 unid.) & Baixo (rolamento) & $\approx$ 60-80 & Bom, mas mais caro \\
Esfera única (móvel) & Baixo (rolamento) & $\approx$ 50 & Útil para pontos localizados \\ \hline
\end{tabular}
\fonte{Elaboração própria com base em cotações (2026).}
\end{table}

A fita de PTFE com skid impresso foi a opção selecionada por apresentar o menor custo total, maior adaptabilidade geométrica e coeficiente de atrito mais baixo entre todas as alternativas.

\end{document}

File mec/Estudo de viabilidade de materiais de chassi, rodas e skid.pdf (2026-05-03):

Estudo de Viabilidade: Materiais para Chassi,

# Rodas e Skid

### Micromouse - Competição de Robôs Autônomos

### Geovana Almeida Miranda Sant’Ana Caio Venâncio do Rosário

### 1 de maio de 2026

### Elaboração do estudo

O presente estudo foi realizado em uma sessão colaborativa na plataforma Dis-

cord, com duração total de 5 horas e 28 minutos. Foram responsáveis pela pesquisa,

consolidação dos dados e redação final:

- Geovana Almeida Miranda Sant’Ana (231027088)
- Caio Venâncio do Rosário (231027195)

Todo o levantamento de coeficientes de atrito, propriedades térmicas dos ma-

teriais e análise de viabilidade técnica e orçamentária foi executado pelos autores

durante o período mencionado.

## 1 Introdução e Objetivo

Este documento avalia a viabilidade de diferentes materiais poliméricos para

três componentes principais de um robô Micromouse: chassi, rodas e skid (patim

deslizante). O estudo considera três cenários de piso: asfalto (caso extremo de alto

atrito), MDF (piso real da competição) e vidro (caso hipotético de baixo atrito).

O robô foi modelado para atingir velocidade de pico de 6 m/s, caracterizando

um cenário de alto desempenho. Materiais aprovados neste cenário são automatica-

mente adequados para robôs mais lentos.

## 2 Metodologia de Cálculo Térmico

A geração de calor por fricção foi estimada pelo modelo de potência dissipada:

P = µ · N · v | (1)

Onde:

- P = potência térmica dissipada [W]
- µ = coeficiente de atrito cinético [adimensional]

- N = força normal (peso do robô) [N]
- v = velocidade [m/s]

Parâmetros adotados:

- Massa do robô: m = 0, 1 kg (100 gramas)
- Força normal: N = m · g = 0, 1 · 9, 81 = 0, 981 N ≈ 1 N
- Velocidade: v = 6 m/s

A Tabela 1 apresenta a potência gerada para diferentes coeficientes de atrito.

Table 1: Potência térmica gerada por fricção a 6 m/s
µ | P (W)
0,05 | 0,30
0,10 | 0,60
0,30 | 1,80
0,50 | 3,00
0,70 | 4,20

Fonte: Elaboração própria (2026).

### Critério de Falha Térmica

Um material falha quando sua superfície atinge a Temperatura de Transição

Vítrea (Tg), passando do estado rígido ao borrachudo, perdendo forma e aumentando

o atrito irreversivelmente. Para elastômeros (TPU), a Tg não é definida, sendo mais

resistentes.

## 3 Análise de Coeficientes de Atrito por Superfície

A Tabela 2 apresenta os coeficientes de atrito estimados para cada material nas

três superfícies analisadas.

## 4 Risco de Falha Térmica a 6 m/s

A Tabela 3 avalia o risco de derretimento/deformação para cada material na

velocidade máxima.

Table 2: Coeficientes de atrito estimados por material e superfície
Material | Asfalto | MDF | Vidro
PLA | 0,4 - 0,5 | 0,5 - 0,6 | 0,3 - 0,4
PETG | 0,3 - 0,4 | 0,4 - 0,5 | 0,15 - 0,25
ABS | 0,5 - 0,6 | 0,4 - 0,55 | 0,2 - 0,3
ASA | 0,5 - 0,6 | 0,4 - 0,55 | 0,2 - 0,3
Nylon | 0,4 - 0,5 | 0,3 - 0,45 | 0,15 - 0,25
TPU | 0,6 - 0,8 | 0,5 - 0,7 | 0,5 - 0,6
PTFE (fita) | 0,05 - 0,10 | 0,04 - 0,08 | 0,04 - 0,07

Fonte: Elaboração própria a partir de dados estimados (2026).

Table 3: Risco de falha térmica a 6 m/s
Material | Tg (°C) | Risco de Falha
PLA | 60 - 65 | ALTO (excede Tg rapidamente)
PETG | 75 - 85 | MODERADO-ALTO
ABS | 105 - 115 | MODERADO
ASA | 110 - 120 | MODERADO
Nylon | 45 - 70* | MODERADO-ALTO (*Tg baixa mas tenacidade alta)
TPU | — | BAIXO (elastômero, dissipa bem)
PTFE | >300 | MUITO BAIXO

Fonte: Elaboração própria com base em fichas técnicas (2026).

## 5 Aplicação por Componente

### 5.1 Chassi

Requisitos: rigidez, resistência ao impacto, baixa deformação térmica.

Table 4: Materiais para chassi - ordem de preferência
Material | Desempenho
ASA | Excelente (rígido, estável, fácil de imprimir)
ABS | Bom (similar ao ASA, porém menos estável)
PETG | Regular (mais flexível, pode torcer)
PLA | Péssimo (frágil, deforma com calor)
TPU | Inadequado (muito flexível)

Fonte: Elaboração própria (2026).

### 5.2 Rodas Motorizadas

Requisitos: alto atrito para aceleração e frenagem.

Table 5: Materiais para rodas - ordem de preferência
Material | Desempenho
TPU | Excelente (maior µ, dissipa calor bem)
ABS/ASA | Bom (atrito médio-alto, alternativas rígidas)
PLA/PETG | Não recomendado (falha térmica ou baixo atrito)

Fonte: Elaboração própria (2026).

### 5.3 Skid (Patim Deslizante)

Requisitos: mínimo atrito, alta resistência ao desgaste.

Table 6: Materiais para skid - ordem de preferência
Material | Desempenho
Fita PTFE (Teflon) | Excelente (µ ≈ 0, 05)
POM (Acetal/Delrin) | Ótimo (µ ≈ 0, 13)
Nylon | Regular (µ ≈ 0, 34)
ASA/ABS | Péssimo (µ ≈ 0, 5)

Fonte: Elaboração própria (2026).

## 6 Recomendação Final para o Projeto

Considerando:

- Impressora disponível: Bambu Lab X1 Carbon (câmara fechada)
- Orçamento: R$ 100 por pessoa (20 pessoas = R$ 2.000 total)
- Desejo de usar um único filamento para chassi + skid
- Rodas adquiridas separadamente (Lego ou comerciais)
- Evitar compósitos devido à anisotropia

### Material Escolhido: ASA (Acrilonitrila Estireno Acrilato)

### Solução Proposta

1. Imprimir chassi em ASA.
2. Imprimir skid em ASA.

Table 7: Justificativa para escolha do ASA
Critério | Avaliação
Custo (1kg) | R$ 120 - 150
Chassi | Excelente (rígido, resistente ao calor)
Skid (puro) | Ruim (alto atrito)
Skid + fita PTFE | Excelente (solução híbrida)
Impressão na X1 Carbon | Ideal (câmara fechada)
Anisotropia | Baixa (diferente de compósitos)

Fonte: Elaboração própria (2026).

3. Colar fita de PTFE (R$ 41,46 por 2 rolos) na superfície de contato do skid.
4. Adquirir rodas prontas (Lego ou rodízios comerciais).

## 7 Orçamento Estimado (20 pessoas)

Table 8: Orçamento detalhado
Item | Valor (R$)
2 kg de ASA (2 rolos de 1kg) | 300
Fita PTFE (2 rolos) | 42
Rodas/rodízios (opção econômica) | ∼ 50
Total | ∼ 392

Fonte: Elaboração própria com base em cotações (2026).

Obs: Orçamento muito abaixo do limite de R$100/pessoa, permitindo folga para

componentes eletrônicos.

## 8 Conclusão

A combinação ASA + fita PTFE atende a todos os requisitos:

- Chassi rígido e resistente termicamente.
- Skid de baixíssimo atrito com a fita.
- Custo acessível para o grupo.
- Aproveitamento máximo da impressora Bambu Lab X1 Carbon.

Alternativa secundária: ABS (mais barato, porém menos estável dimensional-

mente) ou PETG (mais fácil de imprimir, porém chassi menos rígido).

## References

[1] CALLISTER, W. D.; RETHWISCH, D. G. Materials Science and Engineering: An

Introduction. 10. ed. Hoboken: Wiley, 2018.

[2] MATWEB. Propriedades de materiais poliméricos. Disponível em: www.matweb.

com. Acesso em: 30 abr. 2026.

[3] 3D LAB. Fichas técnicas de filamentos ASA, ABS, PETG, PLA, TPU, Nylon.

Disponível em: www.3dlab.com.br. Acesso em: 30 abr. 2026.

[4] BAMBU LAB. Especificações da impressora X1 Carbon. Disponível em: www.

bambulab.com. Acesso em: 30 abr. 2026.

[5] IEEE ROBOTICS AND AUTOMATION SOCIETY. IEEE Micromouse Competition:

Rules and Guidelines. Nova York: IEEE, 2023.

ANEXO A — Levantamento de Componentes para Skid,

## Esferas e Rodízios

Como parte do estudo de viabilidade, foram levantadas opções tanto para man-

ufatura própria (impressão 3D) quanto para aquisição comercial de componentes

de baixo atrito ou rolamento. Os preços foram cotados em dólares (US$) ou reais (R$)

conforme a origem.

### Opções para impressão própria (Thingiverse)

- Suporte para esfera / caster caseiro – arquivo com geometria para alojar esfera

de rolamento. https://www.thingiverse.com/thing:8959

- Skid fixo com base para fixação – modelo simples de patim deslizante para im-

pressão em ABS/ASA ou nylon. https://www.thingiverse.com/thing:3145120

Ambos os projetos podem ser impressos com o filamento ASA escolhido e, se

necessário, receber a fita de PTFE na superfície de contato.

### Componentes comerciais avaliados

Rodízios adesivos (mini casters)

- VXB – 1/2" Mini Swivel Adhesive Caster Wheels (pacote com 8) Pequenos

rodízios giratórios com placa autoadesiva. https://vxb.com/products/1-2in-mini-swivel-adhesive-caster-wheels-8pack

- GNYOHUA – Self-Adhesive Casters (Amazon EUA) Modelo similar, com 8

peças, aplicação leve. https://www.amazon.com/GNYOHUA-Adhesive-Furniture-Appliances-Light-Duty/

dp/B0CXPQSC9R Preço: US$ 9,99 + frete de importação.

Múltiplas esferas ou esfera única

- Esfera única para móvel (transferidor universal) – pode ser adaptada como

ponto de contato de baixo atrito. https://www.amazon.com/Appliance-Universal-Transfers-Furniture-Appliances/

dp/B0D8PHFKRQ Preço: US$ 8,49.

Fita de PTFE (baixíssimo atrito)

- Fita deslizante para gaveta – 1,5 cm x 10 m (2 rolos) Material: PTFE, re-

sistente à abrasão e ao calor. Disponível na Amazon Brasil. Preço: R$ 41,46 (2

rolos).

### Análise de custo-benefício

Table 9: Comparativo entre soluções para baixo atrito
Solução | Atrito estimado | Custo (R$) | Observação
Fita PTFE + skid impresso | Muito baixo (µ ≈ 0, 05) | 20-30 | Mais flexível e barato
Caster adesivo (8 unid.) | Baixo (rolamento) | ≈ 60-80 | Bom, mas mais caro
Esfera única (móvel) | Baixo (rolamento) | ≈ 50 | Útil para pontos localizados

Fonte: Elaboração própria com base em cotações (2026).

A fita de PTFE com skid impresso foi a opção selecionada por apresentar o

menor custo total, maior adaptabilidade geométrica e coeficiente de atrito mais baixo

entre todas as alternativas.

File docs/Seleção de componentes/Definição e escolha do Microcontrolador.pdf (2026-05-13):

# Definição e escolha do Microcontrolador

Após a análise das necessidades do projeto do Micromouse, foi definido o seguinte componente:

- Microcontrolador: ESP32 DevKit

A escolha do ESP32 DevKit baseou-se em critérios técnicos e práticos, resolvendo as principais necessidades de processamento, conectividade e integração de hardware do projeto.

### 1. Explicação da escolha do Microcontrolador

O Micromouse exige um processamento rápido para o mapeamento do labirinto e grande capacidade de integração simultânea com diversos sensores e motores. Desse modo, as seguintes características foram fundamentais para a escolha do ESP32 como o microcontrolador para o projeto:

- Processamento e Memória: O processador dual-core e a ampla disponibilidade de memória SRAM são essenciais para executar algoritmos complexos de mapeamento e resolução de labirintos de forma rápida e eficiente, sem gargalos de memória.
- Ecossistema e Validação: Trata-se de um hardware amplamente validado e utilizado por diversas equipes de competição. A vasta disponibilidade de bibliotecas prontas facilita o desenvolvimento do software e a integração ágil dos módulos que utilizaremos.
- Conectividade Integrada: A arquitetura da placa já possui conectividade Wi-Fi e Bluetooth integradas de forma nativa. Isso elimina a necessidade de adquirir periféricos extras para comunicação sem fio e telemetria, o que barateia e simplifica a lista de componentes do projeto.
- Integração I2C: O ESP32 possui integração nativa e eficiente com o protocolo I2C. Essa interface facilita a comunicação com a grande maioria dos módulos escolhidos para o projeto, permitindo que múltiplos dispositivos sejam conectados compartilhando os mesmos pinos de barramento.
- Disponibilidade de Pinos: A placa possui uma quantidade considerável de pinos de entrada e saída, o que confere a flexibilidade necessária para gerenciar várias funções e periféricos de forma simultânea e centralizada.

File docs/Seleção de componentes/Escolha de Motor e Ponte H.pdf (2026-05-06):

# Escolha de Motor e Ponte H

Após pesquisas e discussões com membros da Frente de Eletrônica, foram escolhidos os seguintes componentes (Motor e Ponte H):

- Motor: Mini Motor Redutor Dc 6v N20 750 Rpm - Com Encoder
- Ponte H: TB6612FNG

A escolha do Motor N20 (750 RPM) em conjunto com o driver TB6612FNG resolve os três principais problemas do micromouse: espaço, peso e controle de velocidade.

## 1. Explicação da escolha do Motor

O Micromouse exige que o motor tenha uma aceleração agressiva para percorrer as retas e uma frenagem precisa para não bater nas paredes.

- Relação Peso/Potência: O motor N20 pesa apenas cerca de 20g. Em um robô que deve ser relativamente leve para um bom desempenho, cada grama economizada nos motores permite colocar baterias maiores ou sensores extras.
- Velocidade (750 RPM): Com uma roda padrão de 34mm, esse motor permite que o robô atinja velocidades próximas a 1,3 m/s. Por causa disso, o motor é rápido o suficiente para ser competitivo, mas não tão rápido que o processador (ESP32) não consiga ler o labirinto a tempo.
- Encoder Acoplado: O encoder magnético na traseira do motor é o que permite o controle preciso da velocidade e posição. Ele informa ao ESP32 exatamente quantos milímetros cada roda percorreu, permitindo curvas de 90° perfeitas e compensação de erro caso uma roda derrape.

## 2. Explicação da escolha da Ponte H

O TB6612FNG foi escolhido por ter as seguintes qualidades:

- Eficiência (Tecnologia MOSFET): Drivers antigos perdem cerca de 2V da bateria apenas para funcionar (calor). O TB6612FNG usa transistores MOSFET, que têm resistência quase nula. Isso significa que toda a energia da sua bateria vai para os motores, aumentando a autonomia e a força.
- Tamanho Miniatura: Ele ocupa menos de 1/4 do espaço de um driver comum, permitindo que o robô seja montado em um chassi muito estreito, permitindo que ele não bata nas paredes laterais do labirinto.
- Frequência de PWM: Ele suporta frequências de PWM de até 100 kHz. Isso permite um controle de velocidade extremamente suave e silencioso, essencial para o ajuste fino do algoritmo PID de navegação.

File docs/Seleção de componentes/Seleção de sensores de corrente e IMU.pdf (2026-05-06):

# Seleção de sensores de corrente

Após a análise das necessidades de gerenciamento de energia e segurança elétrica do projeto do Micromouse, foi definido o seguinte componente:

- Sensor de Corrente e Tensão: Módulo INA226

A escolha do módulo INA226 baseou-se na necessidade de monitorar de forma precisa e constante o consumo de corrente dos motores e a tensão da bateria, protegendo a eletrônica do robô e otimizando o uso da energia.

### 1. Explicação da escolha do módulo INA226

O Micromouse, por ser um robô autônomo e de alta performance, exige um monitoramento de sua fonte de alimentação. Desse modo, as seguintes características foram fundamentais para a escolha do INA226:

- Alta Precisão de Leitura: O INA226 é reconhecido por oferecer medições de altíssima precisão tanto da tensão do barramento quanto da corrente, através da leitura de queda de tensão no resistor shunt. Desse modo, garantindo dados confiáveis do que os obtidos pelos conversores analógico-digitais (ADCs) internos do microcontrolador.
- Integração I2C: Assim como os sensores de distância e outros periféricos do projeto, o INA226 opera via protocolo de comunicação I2C. Isso permite conectá-lo ao mesmo barramento de dados já existente, economizando pinos importantes do ESP32 para outras finalidades.
- Processamento Interno de Potência: O chip possui a capacidade de realizar o cálculo matemático da potência elétrica internamente e entregar o valor pronto via software.

# Seleção de IMU

Após a análise das necessidades de odometria, orientação e controle de estabilidade do projeto do Micromouse, foi definido o seguinte componente:

- IMU (Motion Processing Unit): MPU-9250

A escolha do sensor MPU-9250 baseou-se em requisitos rigorosos de precisão, baixa latência, integração física e eficiência energética, fatores cruciais para a navegação de alta velocidade em ambientes restritos.

### 1. Explicação da escolha do MPU-9250

O robô Micromouse exige um sistema inercial capaz de fornecer dados confiáveis em tempo real para suportar a estimativa de posição, corrigir variações angulares e detectar acelerações bruscas. Devido a essas demandas dinâmicas, as seguintes características justificam a escolha deste componente:

- Integração de 9 Eixos: O sensor combina giroscópio (velocidade angular), acelerômetro (aceleração linear) e magnetômetro (heading absoluto) em um único encapsulamento. Isso elimina a necessidade de múltiplos componentes separados, reduzindo o peso e simplificando o design da placa.
- Processador de Movimento Digital (DMP): Um dos maiores diferenciais do MPU-9250 é o seu DMP integrado em hardware. Ele realiza internamente o processamento e a fusão complexa dos dados dos sensores (como Filtros de Kalman), entregando a orientação já refinada (Quaternions ou Ângulos de Euler).
- Correção de Erros de Integração (Drift): Diferente de soluções comuns de 6 eixos, a presença do magnetômetro no MPU-9250 fornece uma referência absoluta de direção, permitindo o reset da orientação mesmo após grandes erros ao longo do labirinto.
- Conectividade: O componente suporta comunicação via I2C, facilitando a integração no barramento unificado do projeto.
- Eficiência Energética: Apresenta um consumo de corrente tipicamente baixo (cerca de 1.8 mA em modo de operação completo), o que maximiza a vida útil da bateria, permitindo mais tempo de testes e autonomia durante as corridas da competição.

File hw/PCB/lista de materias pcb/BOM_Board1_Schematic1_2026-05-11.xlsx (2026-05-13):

No. | Quantity | Comment | Designator | Footprint | Value | Manufacturer Part | Manufacturer | Supplier Part | Supplier | Pin Count
1 | 3 | KF2EDGR-5.08-8P | CN1,CN4,CN5 | CONN-TH_8P-P5.08_KF2EDGR-5.08-8P |  | KF2EDGR-5.08-8P | KEFA(科发) | C441210 | LCSC | 8
2 | 1 | KF2EDGR-5.08-2P | CN3 | CONN-TH_2P-P5.08_KF2EDGR-5.08-2P |  | KF2EDGR-5.08-2P | KEFA(科发) | C441204 | LCSC | 2
3 | 1 | KF2EDGR-5.08-3P | CN8 | CONN-TH_3P-P5.08_KF2EDGR-5.08-3P |  | KF2EDGR-5.08-3P | KEFA(科发) | C441205 | LCSC | 3
4 | 3 | 100mΩ | R1,R2,R3 | RES-TH_BD5.0-L15.5-P19.50-D0.7 | 100mΩ | MF3WS-0.1Ω±1%T | 华星机电 | C714162 | LCSC | 2
5 | 4 | Screw-Hole-M2 | SCREW1,SCREW2,SCREW3,SCREW4 | Screw-Hole-M2 |  |  |  |  |  | 1
6 | 1 | KCD11 10*15 | SW1 | SW-TH_3P-KCD11-2 |  | KCD11 10*15 |  | C9900004829 | LCSC | 3
7 | 1 | MPU-9250 | U1 | MPU-9250 |  |  |  |  |  | 10
8 | 1 | ESP32 DEVKIT | U2 | ESP32 DEVKIT |  |  |  |  |  | 30
9 | 1 | MP1584EN | U3 | MP1584EN |  |  |  |  |  | 8
10 | 1 | TB6612FNG | U4 | TB6612FNG |  |  |  |  |  | 16
11 | 1 | MicroSDCardAdapter | U5 | MICROSDCARDADAPTER |  |  |  |  |  | 6
12 | 1 | MODULO_INA226 | U6 | MODULO_INA226 |  |  |  |  |  | 10

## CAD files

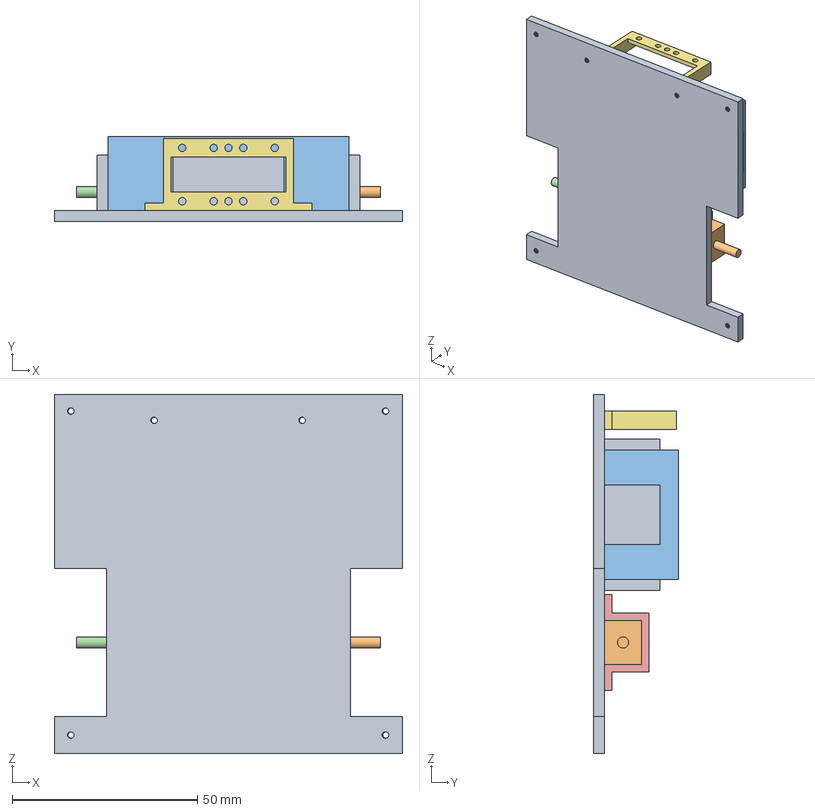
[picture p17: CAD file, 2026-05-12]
mec/modelagem 3d/base/Base-2.4.FCStd
94.0 x 23.0 x 97.0 mm
Motor001
BatteryBlackBox
Motor002
SuporteMotor
SuporteMotor002
SuporteSensor

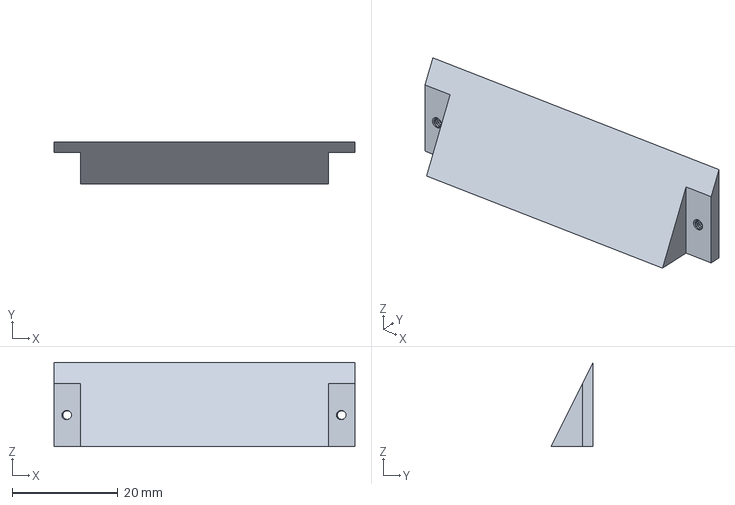
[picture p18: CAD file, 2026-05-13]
mec/modelagem 3d/base/skid/Skid1.0.FCStd
57.0 x 8.00 x 16.0 mm

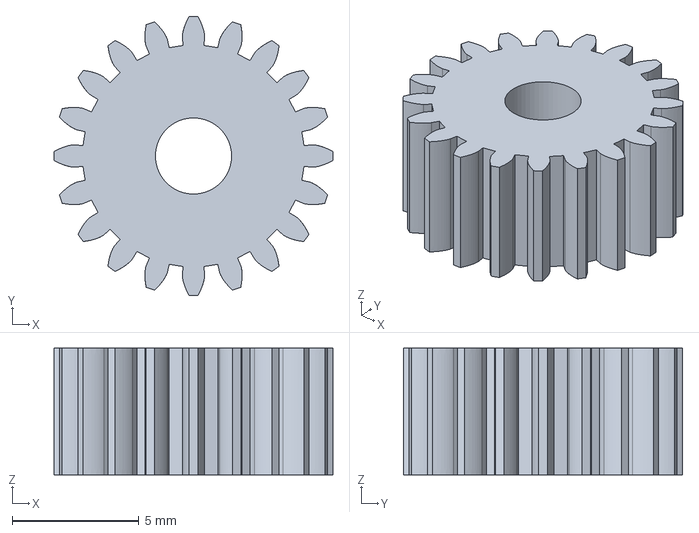
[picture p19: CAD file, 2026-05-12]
mec/modelagem 3d/engrenagem/ENGRENAGEM_MAIOR.FCStd
11.0 x 11.0 x 5.00 mm

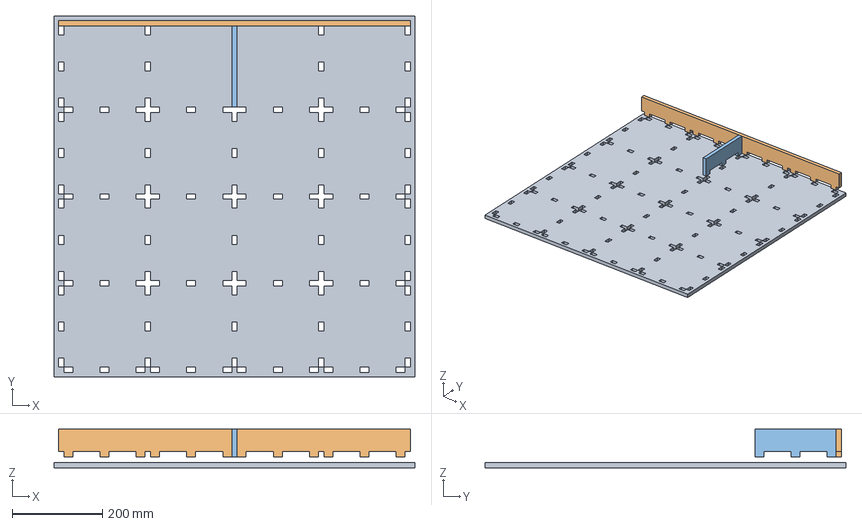
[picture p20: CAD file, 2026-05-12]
mec/modelagem 3d/Labirinto06.FCStd
800.0 x 800.0 x 86.0 mm
Piso
paredeexterna
paredeinterna

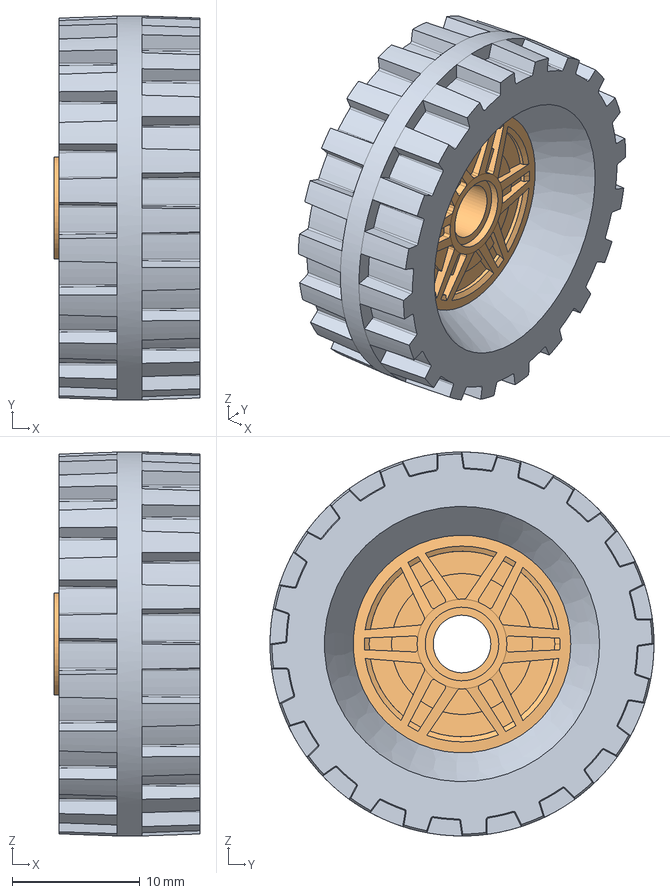
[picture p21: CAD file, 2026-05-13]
mec/modelagem 3d/roda/Roda-1.0.FCStd
11.4 x 30.0 x 30.0 mm
Pneu
Roda

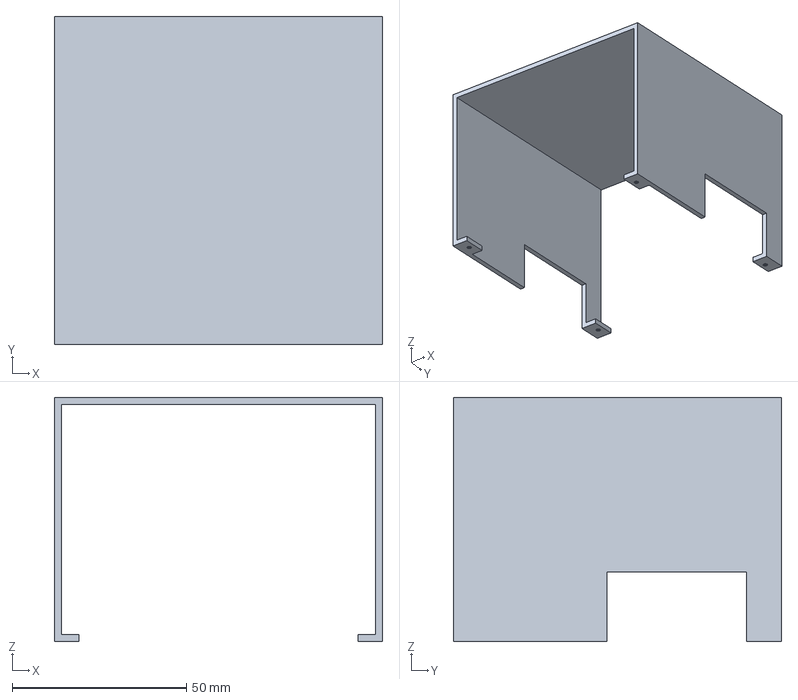
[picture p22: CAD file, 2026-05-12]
mec/modelagem 3d/superior/chassi_superior3.0.FCStd
94.0 x 94.0 x 70.0 mm

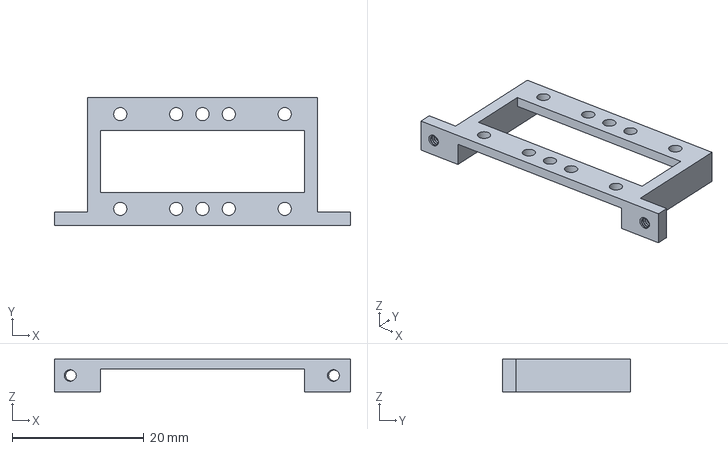
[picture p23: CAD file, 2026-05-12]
mec/modelagem 3d/suportes/SuporteSensor1.0.FCStd
45.0 x 19.4 x 5.00 mm

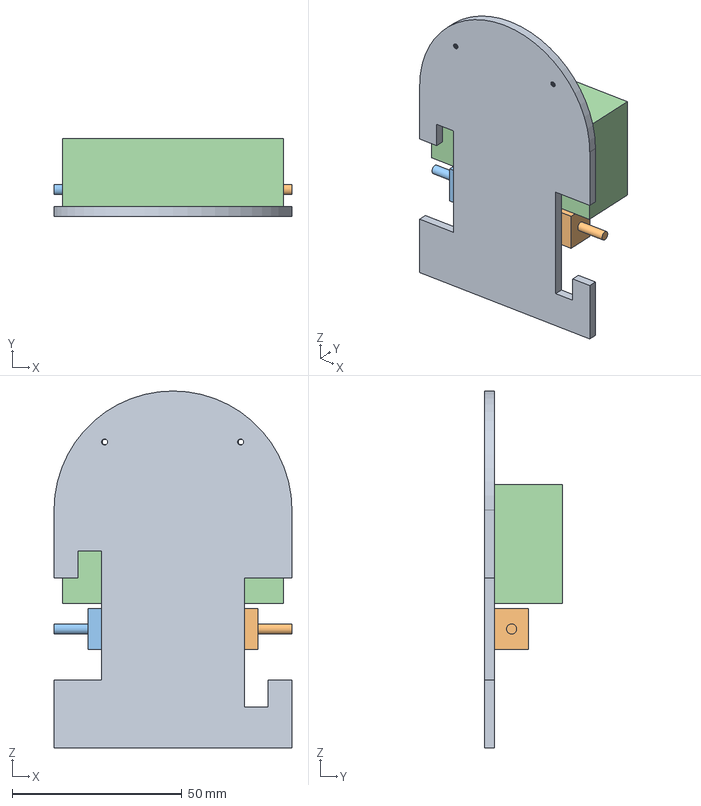
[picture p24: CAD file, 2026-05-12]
mec/modelagem 3d/base/Base-2.2.FCStd
70.0 x 23.0 x 105.0 mm
Motor001
Motor002
BatteryBlackBox

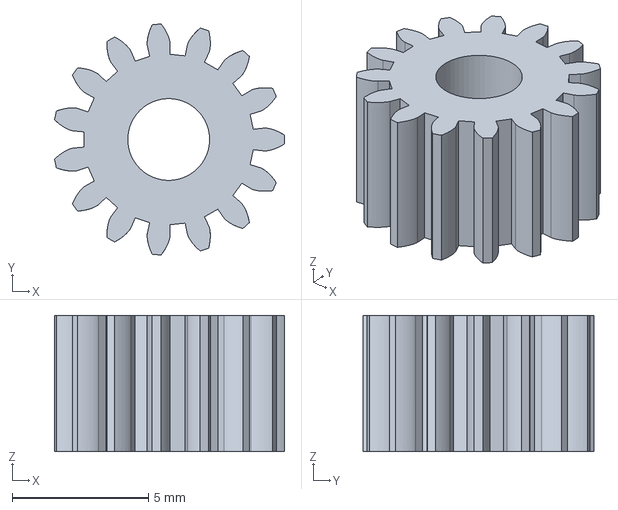
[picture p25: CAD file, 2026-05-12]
mec/modelagem 3d/engrenagem/ENGRENAGEM_MENOR.FCStd
8.43 x 8.48 x 5.00 mm

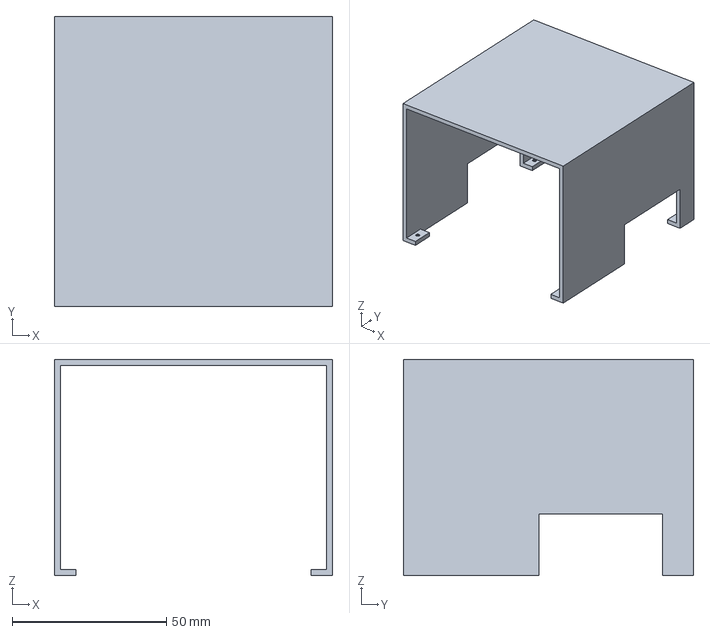
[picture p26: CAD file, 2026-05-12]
mec/modelagem 3d/superior/chassi_superior2.0.FCStd
90.0 x 94.0 x 70.0 mm

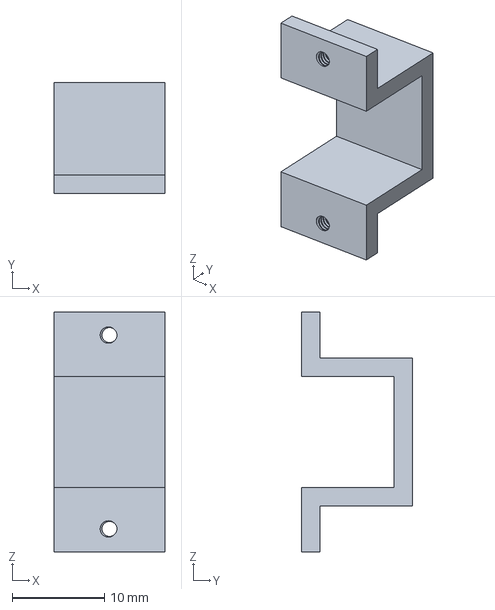
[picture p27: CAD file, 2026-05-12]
mec/modelagem 3d/suportes/SuporteMotor1.0.FCStd
12.0 x 12.0 x 26.0 mm

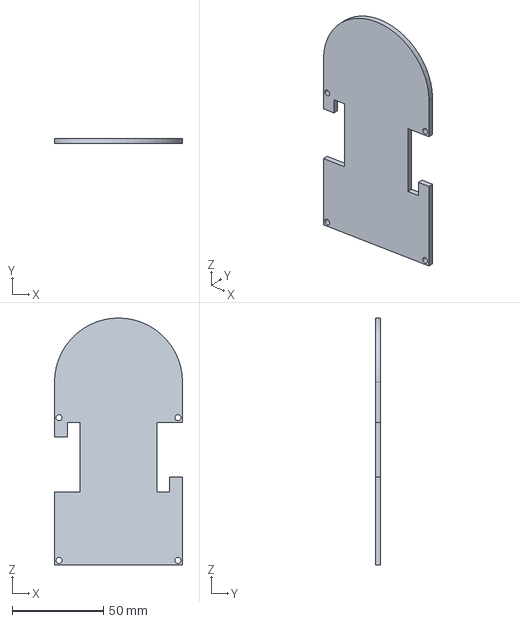
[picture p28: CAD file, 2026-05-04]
mec/modelagem 3d/base/Base.FCStd
70.0 x 3.00 x 135.0 mm

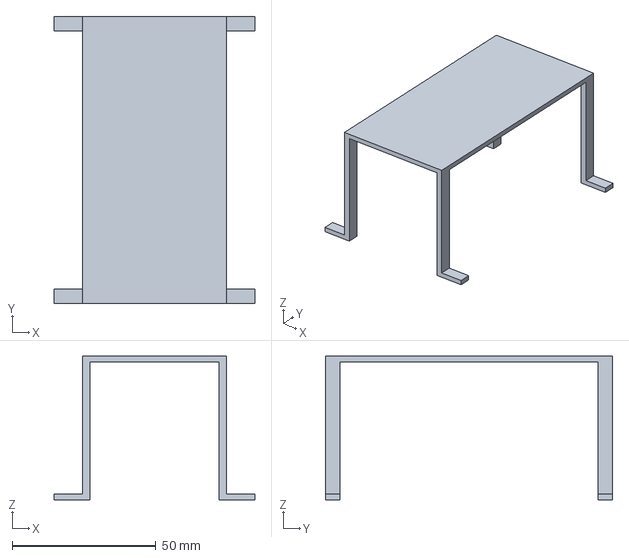
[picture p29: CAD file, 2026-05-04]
mec/modelagem 3d/superior/chassi_superior.FCStd
70.0 x 100.0 x 50.0 mm

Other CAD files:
mec/modelagem 3d/labirinto/Junta_L.CATPart
mec/modelagem 3d/labirinto/Parede_externa_junta_asa.CATPart
mec/modelagem 3d/labirinto/Parede_interna_junta_asa.CATPart
mec/modelagem 3d/labirinto/junta_4_internas.CATPart

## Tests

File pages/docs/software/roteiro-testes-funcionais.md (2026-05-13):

# Roteiro de Testes Funcionais - Software

Este documento define os **casos de teste funcionais** do software do Micromouse, com base nos requisitos e histórias de usuário. Os testes validam as funcionalidades críticas do software, desde a recepção de dados até a visualização e persistência de resultados.

---

### CT-S01 - Recepção de dados do Micromouse

| Parâmetro | Detalhe |
| :--- | :--- |
| **Código do caso de teste** | CT-S01 |
| **Nome do caso de teste** | Recepção de telemetria |
| **Objetivo do caso de teste** | Verificar se o sistema recebe os dados de telemetria do Micromouse com sucesso. |
| **Pré-condições do sistema para o teste ser realizado, quando se aplicar** | Micromouse ligado, conectado à rede e sistema web rodando e aberto. |
| **Descrição dos procedimentos a serem executados para o teste** | 1. Iniciar conexão do sistema com o Micromouse<br>2. Monitorar a porta de recebimento dos dados<br>3. Registrar o comportamento |
| **Resultado esperado para o teste ser aprovado (pós-condição após realizado o teste)** | Dados de telemetria recebidos continuamente, sem falhas ou perda de pacotes. |

### CT-S02 - Validação da telemetria recebida

| Parâmetro | Detalhe |
| :--- | :--- |
| **Código do caso de teste** | CT-S02 |
| **Nome do caso de teste** | Validação de pacotes de dados |
| **Objetivo do caso de teste** | Garantir que o sistema valida corretamente os pacotes recebidos, rejeitando formatos inválidos. |
| **Pré-condições do sistema para o teste ser realizado, quando se aplicar** | Conexão estabelecida entre o sistema e o Micromouse. |
| **Descrição dos procedimentos a serem executados para o teste** | 1. Injetar dados de telemetria (válidos e corrompidos/inválidos)<br>2. Observar o log de processamento do backend<br>3. Registrar o comportamento |
| **Resultado esperado para o teste ser aprovado (pós-condição após realizado o teste)** | O sistema aceita pacotes válidos para processamento e descarta/alerta sobre pacotes inválidos. |

### CT-S03 - Monitoramento em tempo real

| Parâmetro | Detalhe |
| :--- | :--- |
| **Código do caso de teste** | CT-S03 |
| **Nome do caso de teste** | Monitoramento da corrida em tempo real |
| **Objetivo do caso de teste** | Avaliar se a interface web atualiza o estado do Micromouse no labirinto instantaneamente. |
| **Pré-condições do sistema para o teste ser realizado, quando se aplicar** | Sistema recebendo dados válidos de telemetria e dashboard aberto. |
| **Descrição dos procedimentos a serem executados para o teste** | 1. Acessar a tela de monitoramento no app<br>2. Observar a atualização visual da posição e dos sensores<br>3. Registrar o comportamento |
| **Resultado esperado para o teste ser aprovado (pós-condição após realizado o teste)** | A interface gráfica exibe a movimentação do rato no labirinto instantaneamente, sem lag perceptível. |

### CT-S04 - Exibição dos indicadores da corrida

| Parâmetro | Detalhe |
| :--- | :--- |
| **Código do caso de teste** | CT-S04 |
| **Nome do caso de teste** | Exibição de indicadores da corrida |
| **Objetivo do caso de teste** | Confirmar a correta exibição dos indicadores como tempo decorrido, velocidade e status. |
| **Pré-condições do sistema para o teste ser realizado, quando se aplicar** | Micromouse em corrida ativa, comunicando com o sistema. |
| **Descrição dos procedimentos a serem executados para o teste** | 1. Acessar o painel da corrida<br>2. Verificar os valores numéricos e gráficos exibidos<br>3. Registrar o comportamento |
| **Resultado esperado para o teste ser aprovado (pós-condição após realizado o teste)** | Os indicadores refletem os dados exatos do rato em tempo real e de forma legível. |

### CT-S05 - Persistência dos dados finais

| Parâmetro | Detalhe |
| :--- | :--- |
| **Código do caso de teste** | CT-S05 |
| **Nome do caso de teste** | Persistência de corrida finalizada |
| **Objetivo do caso de teste** | Assegurar que os dados totais da corrida e o mapa descoberto são salvos no banco de dados. |
| **Pré-condições do sistema para o teste ser realizado, quando se aplicar** | O percurso do Micromouse foi concluído com sucesso. |
| **Descrição dos procedimentos a serem executados para o teste** | 1. Acionar a conclusão da corrida (via Micromouse ou interface)<br>2. Consultar o banco de dados do sistema<br>3. Registrar o comportamento |
| **Resultado esperado para o teste ser aprovado (pós-condição após realizado o teste)** | Os registros completos da corrida (tempo total, mapa, rota executada) são persistidos. |

### CT-S06 - Consulta por labirinto

| Parâmetro | Detalhe |
| :--- | :--- |
| **Código do caso de teste** | CT-S06 |
| **Nome do caso de teste** | Consulta de resultados por labirinto |
| **Objetivo do caso de teste** | Verificar se é possível filtrar os históricos de corrida para visualizar os dados de um labirinto específico. |
| **Pré-condições do sistema para o teste ser realizado, quando se aplicar** | Existência de dados de corridas persistidos associados a diferentes labirintos. |
| **Descrição dos procedimentos a serem executados para o teste** | 1. Acessar a página de histórico/resultados<br>2. Selecionar e aplicar o filtro por um labirinto alvo<br>3. Registrar o comportamento |
| **Resultado esperado para o teste ser aprovado (pós-condição após realizado o teste)** | O sistema atualiza a listagem exibindo somente as corridas pertencentes ao labirinto pesquisado. |

### CT-S07 - Consulta geral de resultados

| Parâmetro | Detalhe |
| :--- | :--- |
| **Código do caso de teste** | CT-S07 |
| **Nome do caso de teste** | Consulta geral do histórico |
| **Objetivo do caso de teste** | Validar a exibição e a funcionalidade de listagem de todo o histórico de resultados globais. |
| **Pré-condições do sistema para o teste ser realizado, quando se aplicar** | Banco de dados populado com diversas corridas salvas. |
| **Descrição dos procedimentos a serem executados para o teste** | 1. Acessar a tela geral de resultados<br>2. Navegar pela listagem de informações<br>3. Registrar o comportamento |
| **Resultado esperado para o teste ser aprovado (pós-condição após realizado o teste)** | O sistema exibe o histórico integral corretamente, com as informações principais formatadas e precisas. |

### CT-SE01 - Inicialização do barramento I2C

| Parâmetro | Detalhe |
| :--- | :--- |
| **Código do caso de teste** | CT-SE01 |
| **Nome do caso de teste** | Inicialização do barramento I2C compartilhado |
| **Objetivo do caso de teste** | Verificar se o firmware inicializa corretamente o barramento I2C usado pelos sensores do Micromouse. |
| **Pré-condições do sistema para o teste ser realizado, quando se aplicar** | Firmware embarcado compilado e placas/sensores conectados corretamente. |
| **Descrição dos procedimentos a serem executados para o teste** | 1. Ligar o Micromouse<br>2. Observar os logs de inicialização do firmware<br>3. Confirmar a criação do barramento I2C compartilhado<br>4. Registrar o comportamento |
| **Resultado esperado para o teste ser aprovado (pós-condição após realizado o teste)** | O barramento I2C é inicializado com sucesso e fica disponível para os módulos dependentes. |

### CT-SE02 - Leitura da bateria

| Parâmetro | Detalhe |
| :--- | :--- |
| **Código do caso de teste** | CT-SE02 |
| **Nome do caso de teste** | Monitoramento e filtragem da bateria |
| **Objetivo do caso de teste** | Garantir que o módulo de bateria leia tensão, corrente, potência e SOC corretamente. |
| **Pré-condições do sistema para o teste ser realizado, quando se aplicar** | Sensor INA226 funcionando e firmware com o módulo de bateria ativo. |
| **Descrição dos procedimentos a serem executados para o teste** | 1. Energizar o Micromouse<br>2. Acompanhar as leituras geradas pelo módulo de bateria<br>3. Verificar se os valores variam de forma coerente com a alimentação<br>4. Registrar o comportamento |
| **Resultado esperado para o teste ser aprovado (pós-condição após realizado o teste)** | O sistema exibe leituras válidas e filtradas de tensão, corrente, potência e SOC. |

### CT-SE03 - Leitura da IMU

| Parâmetro | Detalhe |
| :--- | :--- |
| **Código do caso de teste** | CT-SE03 |
| **Nome do caso de teste** | Atualização dos dados da IMU |
| **Objetivo do caso de teste** | Verificar se o módulo de IMU atualiza corretamente aceleração, giroscópio e temperatura. |
| **Pré-condições do sistema para o teste ser realizado, quando se aplicar** | Sensor MPU-9250 conectado e firmware com a tarefa de IMU em execução. |
| **Descrição dos procedimentos a serem executados para o teste** | 1. Iniciar o Micromouse<br>2. Observar os logs do módulo de IMU<br>3. Movimentar manualmente a placa para gerar variações nos eixos<br>4. Registrar o comportamento |
| **Resultado esperado para o teste ser aprovado (pós-condição após realizado o teste)** | O firmware lê e atualiza os dados da IMU sem falhas, refletindo mudanças de movimento em tempo real. |

### CT-SE04 - Controle dos motores

| Parâmetro | Detalhe |
| :--- | :--- |
| **Código do caso de teste** | CT-SE04 |
| **Nome do caso de teste** | Controle dos motores e encoders |
| **Objetivo do caso de teste** | Confirmar que o módulo de motor aplica PWM corretamente e contabiliza os pulsos dos encoders. |
| **Pré-condições do sistema para o teste ser realizado, quando se aplicar** | Motores e encoders conectados ao firmware embarcado. |
| **Descrição dos procedimentos a serem executados para o teste** | 1. Ligar o sistema embarcado<br>2. Aplicar comandos de movimentação aos motores<br>3. Observar a resposta física dos motores<br>4. Validar a contagem dos encoders<br>5. Registrar o comportamento |
| **Resultado esperado para o teste ser aprovado (pós-condição após realizado o teste)** | Os motores respondem aos comandos e os encoders contabilizam movimento de forma consistente. |

### CT-SE05 - Leitura do sensor TOF

| Parâmetro | Detalhe |
| :--- | :--- |
| **Código do caso de teste** | CT-SE05 |
| **Nome do caso de teste** | Leitura de distância do sensor VL53L0X |
| **Objetivo do caso de teste** | Verificar se o sensor de distância retorna medidas estáveis e compatíveis com o ambiente. |
| **Pré-condições do sistema para o teste ser realizado, quando se aplicar** | Sensor VL53L0X instalado e operacional, com linha de visão desobstruída. |
| **Descrição dos procedimentos a serem executados para o teste** | 1. Iniciar o firmware<br>2. Observar as leituras de distância do sensor TOF<br>3. Aproximar e afastar um obstáculo<br>4. Registrar o comportamento |
| **Resultado esperado para o teste ser aprovado (pós-condição após realizado o teste)** | As leituras de distância são atualizadas corretamente e acompanham a variação do obstáculo. |

### CT-SE06 - Persistência em cartão SD

| Parâmetro | Detalhe |
| :--- | :--- |
| **Código do caso de teste** | CT-SE06 |
| **Nome do caso de teste** | Gravação de telemetria no cartão SD |
| **Objetivo do caso de teste** | Garantir que o módulo de cartão SD registre os dados de telemetria em arquivo com sucesso. |
| **Pré-condições do sistema para o teste ser realizado, quando se aplicar** | Cartão SD inserido e montado corretamente no sistema. |
| **Descrição dos procedimentos a serem executados para o teste** | 1. Iniciar o firmware com o cartão SD presente<br>2. Gerar telemetria dos sensores e do sistema<br>3. Verificar a criação ou atualização do arquivo CSV<br>4. Registrar o comportamento |
| **Resultado esperado para o teste ser aprovado (pós-condição após realizado o teste)** | Os dados são gravados no arquivo configurado no cartão SD sem perda de registros. |

### CT-SE07 - Integração do firmware principal

| Parâmetro | Detalhe |
| :--- | :--- |
| **Código do caso de teste** | CT-SE07 |
| **Nome do caso de teste** | Integração geral dos módulos embarcados |
| **Objetivo do caso de teste** | Validar se o firmware principal inicializa e coordena corretamente todos os módulos embarcados. |
| **Pré-condições do sistema para o teste ser realizado, quando se aplicar** | Todos os sensores e atuadores montados conforme o hardware do Micromouse. |
| **Descrição dos procedimentos a serem executados para o teste** | 1. Ligar o Micromouse<br>2. Verificar a inicialização conjunta de bateria, IMU, motor, TOF e SD card<br>3. Observar a troca de dados entre as tarefas do firmware<br>4. Registrar o comportamento |
| **Resultado esperado para o teste ser aprovado (pós-condição após realizado o teste)** | O firmware sobe todos os módulos sem travamentos e mantém a operação integrada de forma estável. |

### CT-SE08 - Algoritmo de exploração cega (Frontier Based) até a chegada

| Parâmetro | Detalhe |
| :--- | :--- |
| **Código do caso de teste** | CT-SE08 |
| **Nome do caso de teste** | Exploração Frontier Based até localizar a célula de chegada |
| **Objetivo do caso de teste** | Validar que o Frontier Based explora o labirinto de forma eficiente até encontrar a célula objetivo. |
| **Pré-condições do sistema para o teste ser realizado, quando se aplicar** | Algoritmo Frontier Based implementado no firmware, sensores TOF operacionais, Micromouse no ponto de partida. |
| **Descrição dos procedimentos a serem executados para o teste** | 1. Iniciar o Micromouse no ponto de partida do labirinto<br>2. Ativar o modo de exploração Frontier Based<br>3. Monitorar movimento e exploração das fronteiras do labirinto<br>4. Registrar células visitadas, mapa parcial construído e tempo até localizar chegada<br>5. Validar que o algoritmo detecta a célula de chegada e encerra exploração |
| **Resultado esperado para o teste ser aprovado (pós-condição após realizado o teste)** | O Micromouse localiza e alcança a célula de chegada, explorando sistematicamente sem entrar em loops infinitos. Mapa parcial é construído com precisão. |

### CT-SE09 - Transição para FloodFill após localizar chegada

| Parâmetro | Detalhe |
| :--- | :--- |
| **Código do caso de teste** | CT-SE09 |
| **Nome do caso de teste** | Mudança de Frontier Based para FloodFill na chegada |
| **Objetivo do caso de teste** | Validar que o firmware alterna automaticamente para FloodFill ao detectar a célula de chegada e mapeia o restante do labirinto. |
| **Pré-condições do sistema para o teste ser realizado, quando se aplicar** | CT-SE08 concluído (chegada localizada), mapa parcial armazenado em memória. |
| **Descrição dos procedimentos a serem executados para o teste** | 1. Com Micromouse na célula de chegada, ativar algoritmo de mapeamento completo<br>2. Executar FloodFill a partir da célula de chegada<br>3. Registrar propagação de distâncias para todas as células alcançáveis<br>4. Validar que o mapa é atualizado com paredes não exploradas previamente<br>5. Confirmar que a transição ocorre sem perda de dados do mapa anterior |
| **Resultado esperado para o teste ser aprovado (pós-condição após realizado o teste)** | FloodFill mapeia todas as células alcançáveis com distâncias corretas a partir da chegada, preservando informações do Frontier Based e preparando para cálculo da rota ótima. |

### CT-SE10 - Navegação ótima após mapeamento completo

| Parâmetro | Detalhe |
| :--- | :--- |
| **Código do caso de teste** | CT-SE10 |
| **Nome do caso de teste** | Navegação pelo caminho ótimo calculado |
| **Objetivo do caso de teste** | Validar que o Micromouse navega pelo caminho ótimo (menor distância) do ponto de partida até a chegada. |
| **Pré-condições do sistema para o teste ser realizado, quando se aplicar** | CT-SE09 concluído (mapa completo e distâncias calculadas pelo FloodFill). |
| **Descrição dos procedimentos a serem executados para o teste** | 1. Retornar o Micromouse ao ponto de partida<br>2. Ativar modo de navegação ótima<br>3. Monitorar caminho percorrido e validar que segue as menores distâncias<br>4. Registrar tempo total de execução e número de células percorridas<br>5. Comparar com a distância teórica do mapa FloodFill |
| **Resultado esperado para o teste ser aprovado (pós-condição após realizado o teste)** | Micromouse segue o caminho ótimo sem desvios, alcançando a chegada no tempo mínimo teórico, com margem de erro apenas para movimentos físicos e alinhamento. |

### CT-SE11 - Envio de batch de dados via HTTP

| Parâmetro | Detalhe |
| :--- | :--- |
| **Código do caso de teste** | CT-SE11 |
| **Nome do caso de teste** | Envio de batch de telemetria ao servidor backend |
| **Objetivo do caso de teste** | Validar que o firmware coleta dados de telemetria e os envia em lotes via HTTP para o backend. |
| **Pré-condições do sistema para o teste ser realizado, quando se aplicar** | Micromouse com conectividade de rede (WiFi), backend rodando e acessível, fim de execução ou intervalo de envio atingido. |
| **Descrição dos procedimentos a serem executados para o teste** | 1. Registrar telemetria durante execução (posição, sensores, bateria, etc)<br>2. Aguardar conclusão de batch (após N registros ou fim de corrida)<br>3. Monitorar formação e serialização dos dados em JSON<br>4. Enviar POST HTTP com batch de dados ao servidor<br>5. Validar resposta HTTP (status 200, confirmação de recebimento)<br>6. Verificar se dados chegaram íntegros no backend |
| **Resultado esperado para o teste ser aprovado (pós-condição após realizado o teste)** | Batch é enviado com sucesso via HTTP, servidor responde com confirmação, e todos os registros de telemetria são persistidos sem perda ou corrupção. |

### CT-HW01 - Sistema de energia

| Parâmetro | Detalhe |
| :--- | :--- |
| **Código do caso de teste** | CT-HW01 |
| **Nome do caso de teste** | Funcionamento do regulador de tensão |
| **Objetivo do caso de teste** | Verificar se o regulador MP1584EN fornece 3.3V estável na saída. |
| **Pré-condições do sistema para o teste ser realizado, quando se aplicar** | Placa de PCB montada, bateria conectada (12V nominal), multímetro calibrado. |
| **Descrição dos procedimentos a serem executados para o teste** | 1. Conectar bateria ao conector CN3 (BATERIA)<br>2. Medir tensão de saída do regulador (pinos VCC)<br>3. Variar carga conectando/desconectando módulos<br>4. Registrar variações de tensão |
| **Resultado esperado para o teste ser aprovado (pós-condição após realizado o teste)** | Tensão de saída = 3.3V ±5% em regime permanente, ripple < 100mV em transiente. |

### CT-HW02 - Subsistema de gestão energética (INA226)

| Parâmetro | Detalhe |
| :--- | :--- |
| **Código do caso de teste** | CT-HW02 |
| **Nome do caso de teste** | Leitura correta de tensão, corrente e potência da bateria |
| **Objetivo do caso de teste** | Validar que o sensor INA226 mede com precisão as métricas de consumo de energia. |
| **Pré-condições do sistema para o teste ser realizado, quando se aplicar** | Sensor INA226 soldado no módulo, conectado ao barramento I2C, bateria conectada. |
| **Descrição dos procedimentos a serem executados para o teste** | 1. Ligar o ESP32 e ler valores do INA226 via barramento I2C<br>2. Medir tensão com multímetro e comparar com leitura do INA226<br>3. Aplicar diferentes cargas aos motores<br>4. Verificar variação de corrente e potência |
| **Resultado esperado para o teste ser aprovado (pós-condição após realizado o teste)** | Leituras do INA226 coincidem com multímetro (±2%), e responde adequadamente a variações de carga. |

### CT-HW03 - Subsistema de navegação inercial (MPU-9250)

| Parâmetro | Detalhe |
| :--- | :--- |
| **Código do caso de teste** | CT-HW03 |
| **Nome do caso de teste** | Comunicação I2C e leitura do MPU-9250 |
| **Objetivo do caso de teste** | Garantir que o sensor MPU-9250 comunica corretamente via I2C e retorna dados válidos. |
| **Pré-condições do sistema para o teste ser realizado, quando se aplicar** | Sensor MPU-9250 soldado na placa, alimentação em 3.3V, barramento I2C operacional. |
| **Descrição dos procedimentos a serem executados para o teste** | 1. Energizar a placa<br>2. Verificar presença do dispositivo no barramento I2C (endereço 0x68)<br>3. Ler registros de aceleração, giroscópio e temperatura<br>4. Movimentar a placa e verificar mudanças nos eixos XYZ |
| **Resultado esperado para o teste ser aprovado (pós-condição após realizado o teste)** | Comunicação I2C estabelecida, dados de aceleração/giroscópio coerentes com movimento físico. |

### CT-HW04 - Subsistema infravermelho (VL53L0X)

| Parâmetro | Detalhe |
| :--- | :--- |
| **Código do caso de teste** | CT-HW04 |
| **Nome do caso de teste** | Funcionamento dos sensores de distância VL53L0X |
| **Objetivo do caso de teste** | Validar que cada sensor VL53L0X (CN4, CN5 com XSHUT controle) retorna leituras de distância confiáveis. |
| **Pré-condições do sistema para o teste ser realizado, quando se aplicar** | Sensores VL53L0X instalados nos conectores CN4 e CN5, barramento I2C operacional, ESP32 ligado. |
| **Descrição dos procedimentos a serem executados para o teste** | 1. Energizar o sistema<br>2. Ativar cada sensor via pino XSHUT<br>3. Ler valores de distância para obstáculos a 10cm, 20cm e 30cm<br>4. Registrar precisão e tempo de resposta |
| **Resultado esperado para o teste ser aprovado (pós-condição após realizado o teste)** | Ambos os sensores retornam leituras dentro de ±10% do valor real, com resposta < 100ms. |

### CT-HW05 - Subsistema de motores (TB6612FNG)

| Parâmetro | Detalhe |
| :--- | :--- |
| **Código do caso de teste** | CT-HW05 |
| **Nome do caso de teste** | Controle de motores via ponte H TB6612FNG |
| **Objetivo do caso de teste** | Confirmar que a ponte H comuta corretamente e os motores executam movimentos em ambas as direções. |
| **Pré-condições do sistema para o teste ser realizado, quando se aplicar** | TB6612FNG soldado, motores conectados em M1 e M2, encoders instalados, ESP32 ligado. |
| **Descrição dos procedimentos a serem executados para o teste** | 1. Aplicar PWM a AI1/PWMA (motor esquerdo) com variação de duty cycle (0%-100%)<br>2. Aplicar PWM a BI1/PWMB (motor direito) com variação de duty cycle<br>3. Testar sentidos de rotação (AI2, BI2 controlam direção)<br>4. Validar leitura dos encoders para cada movimento |
| **Resultado esperado para o teste ser aprovado (pós-condição após realizado o teste)** | Motores respondem aos comandos PWM, giram em ambas as direções e encoders contabilizam pulsos consistentemente. |

### CT-HW06 - Subsistema de microSD

| Parâmetro | Detalhe |
| :--- | :--- |
| **Código do caso de teste** | CT-HW06 |
| **Nome do caso de teste** | Comunicação SPI e funcionamento do cartão SD |
| **Objetivo do caso de teste** | Validar que o cartão SD comunica via SPI e permite leitura/escrita de arquivos. |
| **Pré-condições do sistema para o teste ser realizado, quando se aplicar** | Adaptador microSD (CN1) montado, cartão SD formatado em FAT32, ESP32 ligado. |
| **Descrição dos procedimentos a serem executados para o teste** | 1. Energizar o sistema<br>2. Inicializar o barramento SPI (CS, SCK, MOSI, MISO)<br>3. Detectar cartão SD<br>4. Criar/escrever arquivo de teste<br>5. Verificar integridade dos dados |
| **Resultado esperado para o teste ser aprovado (pós-condição após realizado o teste)** | Cartão é detectado corretamente, arquivos são escritos e lidos sem corrupção de dados. |
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

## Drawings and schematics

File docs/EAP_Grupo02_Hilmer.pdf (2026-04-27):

# MICROMOUSE

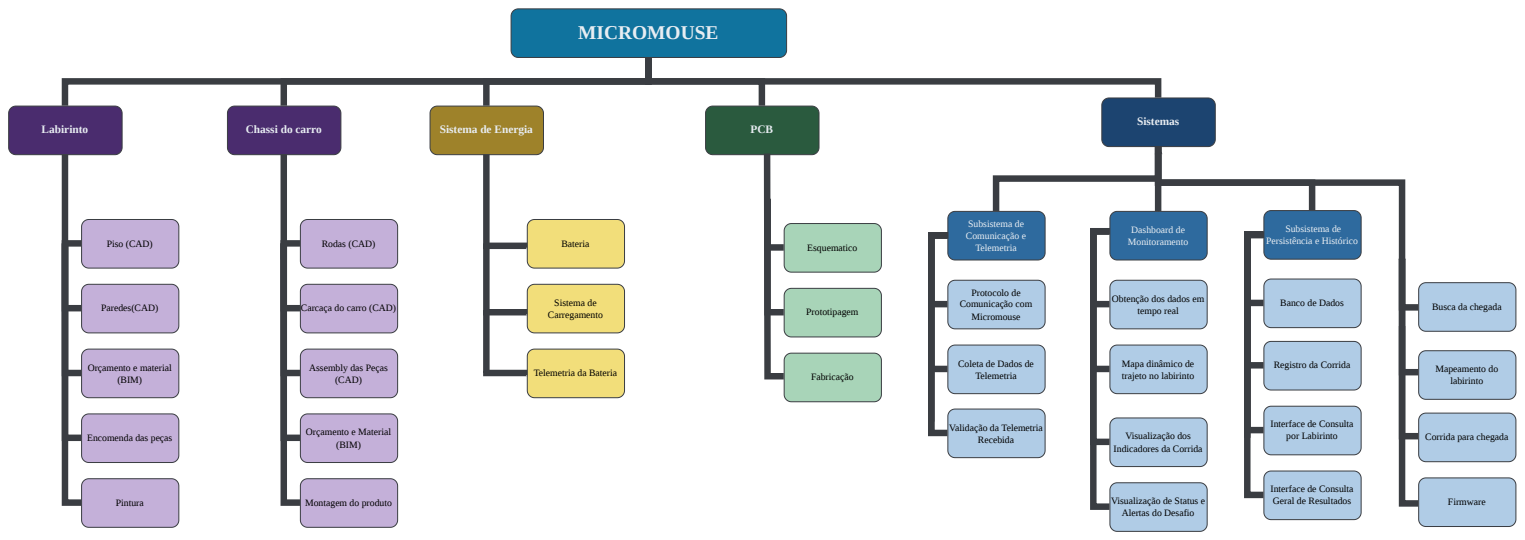
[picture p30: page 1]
Labirinto; Chassi do carro; Sistemas; Sistema de Energia; PCB; Piso (CAD); Paredes(CAD); Orçamento e material (BIM); Pintura; Firmware; Esquematico; Subsistema de Comunicação e Telemetria; Prototipagem; Monitoramento; Persistência e Histórico; Protocolo de Comunicação com Micromouse; Fabricação; Rodas (CAD); Orçamento e Material (BIM); Registro da Corrida; Mapeamento do; labirinto; Bateria; Sistema de Carregamento

Subsistema de

Dashboard de

Obtenção dos dados em
tempo real

Banco de Dados

Carcaça do carro (CAD)

Busca da chegada

Assembly das Peças
(CAD)

Coleta de Dados de
Telemetria

Mapa dinâmico de
trajeto no labirinto

Telemetria da Bateria

Validação da Telemetria
Recebida

Interface de Consulta
por Labirinto

Encomenda das peças

Visualização dos
Indicadores da Corrida

Corrida para chegada

Geral de Resultados

Montagem do produto

Visualização de Status e
Alertas do Desafio

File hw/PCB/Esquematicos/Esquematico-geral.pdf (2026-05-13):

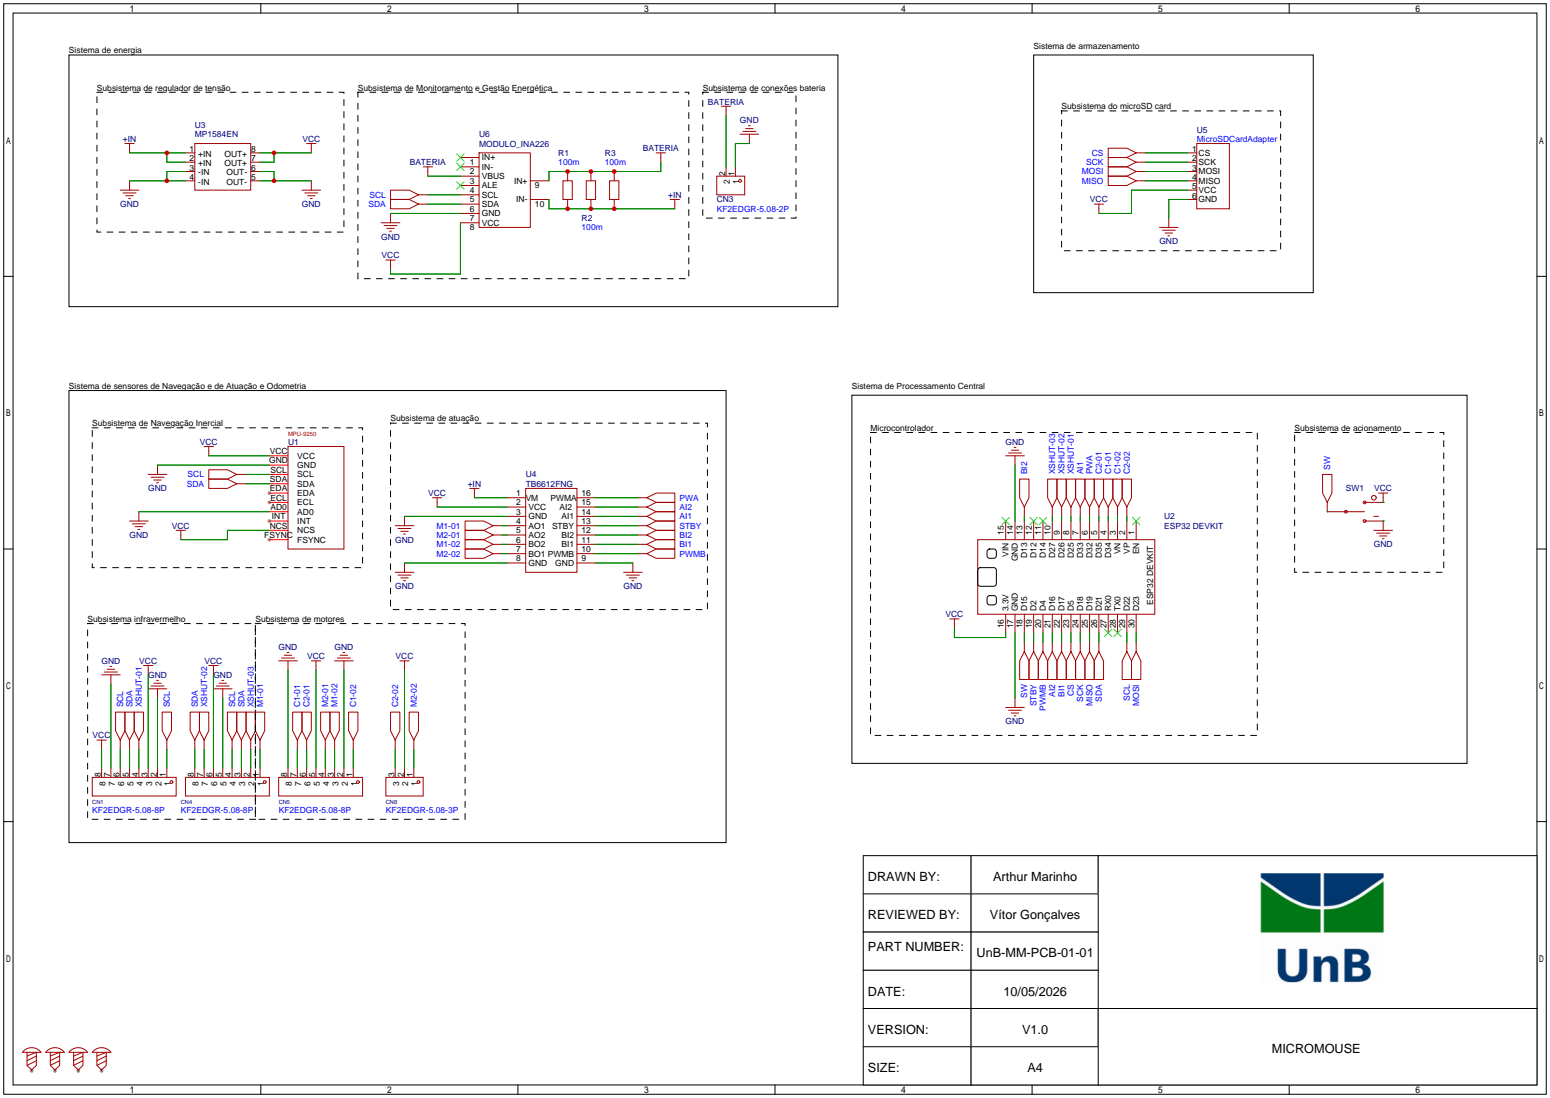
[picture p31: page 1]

Subsistema de regulador de tensão

Subsistema de Monitoramento e Gestão Energética

Subsistema de conexões bateria
BATERIA
GND

Subsistema do microSD card

Subsistema de Navegação Inercial

DRAWN BY: | Arthur Marinho

REVIEWED BY: | Vítor Gonçalves
PART NUMBER: | UnB-MM-PCB-01-01

DATE: | 10/05/2026

VERSION: | V1.0 | MICROMOUSE

SIZE: | A4

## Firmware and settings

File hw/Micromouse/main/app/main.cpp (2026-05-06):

#include <cstdio>
#include <cstring>

#include "battery/battery.hpp"
#include "driver/ledc.h"
#include "freertos/FreeRTOS.h"
#include "freertos/queue.h"
#include "freertos/task.h"
#include "imu.h"
#include "motor/motor.hpp"
#include "pins.hpp"
#include "sd_card.hpp"
#include "vl53l0x/IV_Vl53l0x.hpp"

namespace {

Battery g_battery;
IV_Vl53l0x g_tof;
Motor *g_motor_left = nullptr;
Motor *g_motor_right = nullptr;
volatile float g_tof_distance_mm = -1.0f;

struct BatterySnapshot {
    float voltage;
    float current;
    float power;
    float soc;
};

struct ImuSnapshot {
    DadosIMU data;
    bool valid;
};

portMUX_TYPE g_battery_snapshot_mux = portMUX_INITIALIZER_UNLOCKED;
portMUX_TYPE g_imu_snapshot_mux = portMUX_INITIALIZER_UNLOCKED;
BatterySnapshot g_battery_snapshot = {};
DadosIMU g_imu_snapshot = {};
bool g_imu_snapshot_valid = false;

// Fila para dados -> SD
QueueHandle_t g_data_queue = nullptr;


void cacheBatterySnapshot() {
    portENTER_CRITICAL(&g_battery_snapshot_mux);
    g_battery_snapshot = {
        g_battery.getVoltageFiltered(),
        g_battery.getCurrentFiltered(),
        g_battery.getPowerFiltered(),
        g_battery.getSOC(),
    };
    portEXIT_CRITICAL(&g_battery_snapshot_mux);
}


void cacheImuSnapshot(const DadosIMU &dados) {
    portENTER_CRITICAL(&g_imu_snapshot_mux);
    g_imu_snapshot = dados;
    g_imu_snapshot_valid = true;
    portEXIT_CRITICAL(&g_imu_snapshot_mux);
}


void battery_task(void *) {
    const TickType_t delay = pdMS_TO_TICKS(500);

    while (true) {
        g_battery.update();
        cacheBatterySnapshot();

        BatterySnapshot snapshot = {};
        portENTER_CRITICAL(&g_battery_snapshot_mux);
        snapshot = g_battery_snapshot;
        portEXIT_CRITICAL(&g_battery_snapshot_mux);

        std::printf("Battery -> V: %.2f I: %.2f P: %.2f SOC: %.1f%%\n",
                    snapshot.voltage,
                    snapshot.current,
                    snapshot.power,
                    snapshot.soc);
        vTaskDelay(delay);
    }
}

void imu_task(void *) {
    const TickType_t delay = pdMS_TO_TICKS(100);

    while (true) {
        if (imu_update()) {
            const DadosIMU dados = imu_get_dados();
            cacheImuSnapshot(dados);
            std::printf("IMU -> Accel[%.2f %.2f %.2f] Gyro[%.2f %.2f %.2f] Temp: %.2f\n",
                        dados.accel_x, dados.accel_y, dados.accel_z,
                        dados.gyro_x, dados.gyro_y, dados.gyro_z,
                        dados.temperatura);
        } else {
            std::printf("Falha ao atualizar IMU\n");
        }

        vTaskDelay(delay);
    }
}

void tof_task(void *) {
    const TickType_t delay = pdMS_TO_TICKS(200);

    while (true) {
        const float distance_mm = g_tof.readDistanceMm();
        g_tof_distance_mm = distance_mm;
        std::printf("VL53L0X -> Distancia: %.2f mm\n", distance_mm);
        vTaskDelay(delay);
    }
}


void motor_task(void *) {
    const TickType_t delay = pdMS_TO_TICKS(250);

    // Lógica de movimento será adicionada depois
    while (true) {
        if (g_motor_left && g_motor_right) {
            const int enc_left = g_motor_left->getEncoderCount();
            const int enc_right = g_motor_right->getEncoderCount();
            std::printf("Motors -> Left encoder: %d | Right encoder: %d\n", enc_left, enc_right);
        }
        vTaskDelay(delay);
    }
}


void data_aggregation_task(void *) {
    const TickType_t delay = pdMS_TO_TICKS(500);
    static uint32_t tick_ms = 0;

    while (true) {
        if (!g_data_queue) {
            vTaskDelay(delay);
            continue;
        }

        // Coleta dados de todos os sensores
        RobotData data = {};
        data.timestamp_ms = tick_ms;
        data.distancia_tof[0] = static_cast<int>(g_tof_distance_mm);
        data.distancia_tof[1] = 0;
        data.distancia_tof[2] = 0;
        data.distancia_tof[3] = 0;
        BatterySnapshot battery_snapshot = {};
        portENTER_CRITICAL(&g_battery_snapshot_mux);
        battery_snapshot = g_battery_snapshot;
        portEXIT_CRITICAL(&g_battery_snapshot_mux);
        data.battery_v = battery_snapshot.voltage;
        data.battery_i = battery_snapshot.current;
        data.battery_power = battery_snapshot.power;
        data.battery_soc = battery_snapshot.soc;

        DadosIMU imu_snapshot = {};
        bool imu_snapshot_valid = false;
        portENTER_CRITICAL(&g_imu_snapshot_mux);
        imu_snapshot = g_imu_snapshot;
        imu_snapshot_valid = g_imu_snapshot_valid;
        portEXIT_CRITICAL(&g_imu_snapshot_mux);

        if (imu_snapshot_valid) {
            data.accel_x = imu_snapshot.accel_x;
            data.accel_y = imu_snapshot.accel_y;
            data.accel_z = imu_snapshot.accel_z;
            data.gyro_x = imu_snapshot.gyro_x;
            data.gyro_y = imu_snapshot.gyro_y;
            data.gyro_z = imu_snapshot.gyro_z;
            data.imu_temp = imu_snapshot.temperatura;
        }

        if (g_motor_left && g_motor_right) {
            data.encoder_left = g_motor_left->getEncoderCount();
            data.encoder_right = g_motor_right->getEncoderCount();
        }

        // Enfileira os dados para o SD processar
        if (xQueueSend(g_data_queue, &data, pdMS_TO_TICKS(10)) != pdTRUE) {
            std::printf("[AVISO] Fila de dados cheia, registro descartado\n");
        }

        tick_ms += (uint32_t)delay;
        vTaskDelay(delay);
    }
}

extern "C" void app_main(void) {
    std::printf("=== Micromouse Startup ===\n");
    std::printf("Inicializando módulos...\n");

    // Inicialização de Sensores I2C
    if (!g_battery.init()) {
        std::printf("[ERRO] Falha ao inicializar bateria\n");
        return;
    }
    std::printf("[OK] Bateria inicializada\n");

    if (!imu_init()) {
        std::printf("[ERRO] Falha ao inicializar IMU\n");
        return;
    }
    std::printf("[OK] IMU inicializada\n");

    if (!g_tof.init()) {
        std::printf("[ERRO] Falha ao inicializar VL53L0X\n");
        return;
    }
    std::printf("[OK] VL53L0X inicializado\n");

    if (!g_tof.startRanging()) {
        std::printf("[ERRO] Falha ao iniciar ranging do VL53L0X\n");
        return;
    }
    std::printf("[OK] VL53L0X ranging iniciado\n");

    // Inicialização de Motores
    ledc_timer_config_t ledc_timer = {};
    ledc_timer.speed_mode = LEDC_LOW_SPEED_MODE;
    ledc_timer.timer_num = LEDC_TIMER_0;
    ledc_timer.duty_resolution = LEDC_TIMER_10_BIT;
    ledc_timer.freq_hz = 20000;
    ledc_timer.clk_cfg = LEDC_AUTO_CLK;
    if (ledc_timer_config(&ledc_timer) != ESP_OK) {
        std::printf("[ERRO] Falha ao configurar PWM timer\n");
        return;
    }
    std::printf("[OK] PWM timer configurado\n");

    // Motor Esquerdo: PWM=18, IN1=19, IN2=26, STBY=4, ENCA=32, ENCB=33, Canal PWM 0
    g_motor_left = new Motor(18, 19, 26, (int)MOTOR_STBY_PIN, 32, 33, LEDC_CHANNEL_0);
    g_motor_left->begin();
    std::printf("[OK] Motor esquerdo inicializado\n");

    // Motor Direito: PWM=23, IN1=27, IN2=16, STBY=4, ENCA=25, ENCB=17, Canal PWM 1
    g_motor_right = new Motor(23, 27, 16, (int)MOTOR_STBY_PIN, 25, 17, LEDC_CHANNEL_1);
    g_motor_right->begin();
    std::printf("[OK] Motor direito inicializado\n");

    // Criação de Fila de Dados
    g_data_queue = xQueueCreate(50, sizeof(RobotData));
    if (!g_data_queue) {
        std::printf("[ERRO] Falha ao criar fila de dados\n");
        return;
    }
    std::printf("[OK] Fila de dados criada\n");

    // Inicialização do SD Card (passa a fila compartilhada)
    sdCardInit(g_data_queue);
    if (!estaCartaoSDOk()) {
        std::printf("[AVISO] Cartão SD não disponível; lançando tasks mesmo assim\n");
    } else {
        std::printf("[OK] Cartão SD inicializado\n");
    }

    // Criação de Tasks
    std::printf("\nLançando tasks...\n");

    xTaskCreatePinnedToCore(battery_task, "battery_task", 4096, nullptr, 3, nullptr, 1);
    std::printf("[OK] Task de bateria criada\n");

    xTaskCreatePinnedToCore(imu_task, "imu_task", 4096, nullptr, 3, nullptr, 1);
    std::printf("[OK] Task de IMU criada\n");

    xTaskCreatePinnedToCore(tof_task, "tof_task", 4096, nullptr, 3, nullptr, 1);
    std::printf("[OK] Task de ToF criada\n");

    xTaskCreatePinnedToCore(motor_task, "motor_task", 4096, nullptr, 3, nullptr, 0);
    std::printf("[OK] Task de motores criada\n");

    xTaskCreatePinnedToCore(data_aggregation_task, "data_agg_task", 8192, nullptr, 4, nullptr, 1);
    std::printf("[OK] Task de agregação de dados criada\n");

    std::printf("\n=== Sistema Pronto ===\n");
    std::printf("Micromouse executando em multithread.\n\n");

    // Task raiz aguarda indefinidamente
    while (true) {
        vTaskDelay(portMAX_DELAY);
    }
}
} // namespace

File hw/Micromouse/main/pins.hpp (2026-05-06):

#pragma once

#include "driver/gpio.h"

// I2C (IMU, INA226, VL53L0X)
#define I2C_SDA_PIN GPIO_NUM_21
#define I2C_SCL_PIN GPIO_NUM_22

// SD (SPI)
#define SD_SCK_PIN  GPIO_NUM_14
#define SD_MISO_PIN GPIO_NUM_12
#define SD_MOSI_PIN GPIO_NUM_13
#define SD_CS_PIN   GPIO_NUM_15

// Motor
#define MOTOR_STBY_PIN GPIO_NUM_4

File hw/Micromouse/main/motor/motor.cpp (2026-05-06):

#include "motor/motor.hpp"

Motor::Motor(int pwm, int ain1, int ain2, int stby, int enc_a, int enc_b, ledc_channel_t channel)
    : pwm_pin((gpio_num_t)pwm),
      ain1_pin((gpio_num_t)ain1),
      ain2_pin((gpio_num_t)ain2),
      stby_pin((gpio_num_t)stby),
      enc_a_pin((gpio_num_t)enc_a),
      enc_b_pin((gpio_num_t)enc_b),
      pwm_channel(channel),
      pcnt_unit(NULL) {}

void Motor::begin() {
    // 1. Configura os Pinos Digitais (Direcao e Standby)
    gpio_config_t io_conf = {};
    io_conf.pin_bit_mask = (1ULL << ain1_pin) | (1ULL << ain2_pin) | (1ULL << stby_pin);
    io_conf.mode = GPIO_MODE_OUTPUT;
    io_conf.pull_up_en = GPIO_PULLUP_DISABLE;
    io_conf.pull_down_en = GPIO_PULLDOWN_DISABLE;
    io_conf.intr_type = GPIO_INTR_DISABLE;
    gpio_config(&io_conf);

    // Tira o driver do modo de economia de energia
    gpio_set_level(stby_pin, 1);

    // 2. Configura o Canal do PWM
    ledc_channel_config_t ledc_channel_cfg = {};
    ledc_channel_cfg.speed_mode = LEDC_LOW_SPEED_MODE;
    ledc_channel_cfg.channel = pwm_channel;
    ledc_channel_cfg.timer_sel = LEDC_TIMER_0; // Compartilha o mesmo timer
    ledc_channel_cfg.intr_type = LEDC_INTR_DISABLE;
    ledc_channel_cfg.gpio_num = pwm_pin;
    ledc_channel_cfg.duty = 0;
    ledc_channel_cfg.hpoint = 0;
    ledc_channel_config(&ledc_channel_cfg);

    // 3. Configura o Hardware do Encoder (PCNT)
    pcnt_unit_config_t unit_config = {};
    unit_config.high_limit = 30000;
    unit_config.low_limit = -30000;
    pcnt_new_unit(&unit_config, &pcnt_unit);

    pcnt_glitch_filter_config_t filter_config = {};
    filter_config.max_glitch_ns = 1000;
    pcnt_unit_set_glitch_filter(pcnt_unit, &filter_config);

    pcnt_chan_config_t chan_a_config = {};
    chan_a_config.edge_gpio_num = enc_a_pin;
    chan_a_config.level_gpio_num = enc_b_pin;
    pcnt_channel_handle_t pcnt_chan_a = NULL;
    pcnt_new_channel(pcnt_unit, &chan_a_config, &pcnt_chan_a);

    pcnt_chan_config_t chan_b_config = {};
    chan_b_config.edge_gpio_num = enc_b_pin;
    chan_b_config.level_gpio_num = enc_a_pin;
    pcnt_channel_handle_t pcnt_chan_b = NULL;
    pcnt_new_channel(pcnt_unit, &chan_b_config, &pcnt_chan_b);

    pcnt_channel_set_edge_action(
        pcnt_chan_a,
        PCNT_CHANNEL_EDGE_ACTION_DECREASE,
        PCNT_CHANNEL_EDGE_ACTION_INCREASE
    );
    pcnt_channel_set_level_action(
        pcnt_chan_a,
        PCNT_CHANNEL_LEVEL_ACTION_KEEP,
        PCNT_CHANNEL_LEVEL_ACTION_INVERSE
    );

    pcnt_channel_set_edge_action(
        pcnt_chan_b,
        PCNT_CHANNEL_EDGE_ACTION_INCREASE,
        PCNT_CHANNEL_EDGE_ACTION_DECREASE
    );
    pcnt_channel_set_level_action(
        pcnt_chan_b,
        PCNT_CHANNEL_LEVEL_ACTION_KEEP,
        PCNT_CHANNEL_LEVEL_ACTION_INVERSE
    );

    pcnt_unit_enable(pcnt_unit);
    pcnt_unit_clear_count(pcnt_unit);
    pcnt_unit_start(pcnt_unit);
}

void Motor::setSpeed(int speed) {
    if (speed > 0) {
        gpio_set_level(ain1_pin, 1);
        gpio_set_level(ain2_pin, 0);
    } else if (speed < 0) {
        gpio_set_level(ain1_pin, 0);
        gpio_set_level(ain2_pin, 1);
        speed = -speed; // Transforma em positivo
    } else {
        // Freio (Brake)
        gpio_set_level(ain1_pin, 1);
        gpio_set_level(ain2_pin, 1);
    }

    if (speed > 1023) speed = 1023;

    ledc_set_duty(LEDC_LOW_SPEED_MODE, pwm_channel, speed);
    ledc_update_duty(LEDC_LOW_SPEED_MODE, pwm_channel);
}

int Motor::getEncoderCount() {
    int count = 0;
    pcnt_unit_get_count(pcnt_unit, &count);
    return count;
}

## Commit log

2026-04-16 Documentação inicial do EAP_Estrutura
    Added detailed structure documentation for EAP project including materials and activities for various components.
2026-04-16 Add initial project documentation for EAP structures
    Document the initial structure and materials for the EAP project, including detailed activities for each component.
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2026-04-19 docs: especificação da seção Projeto do EAP de energia
2026-04-19 docs(EAP_Energia): Adiciona a seção de selção dos componentes de energia
2026-04-21 Criação da EAP inicial de Eletrônica
    Divisão de tarefas do projeto para o núcleo de eletrônica
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2026-04-27 feat: Código Esp32
    Criação do projeto do código da esp32
2026-04-30 fix: renderização de sidebar nas pages
2026-04-30 feat: Código INA226
    Primeira versão do código e configurações iniciais para o uso do INA226 com o ESP32
2026-05-01 docs: adicionar documentação aos arquivos battery.hpp e battery.cpp
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2026-05-03 docs(chassi): adicionar estudo de materiais para deslizador e chassi
    feat: adicionar comentários extras no .tex e documento em pdf
2026-05-04 Modelos 3d iniciais da base e parte superior
    [Base.FCStd, chassi_superior.FCStd]
2026-05-04 Rename mec/Captura de tela 2026-05-03 171905.png to mec/modelagem 3d/superior/Captura de tela 2026-05-03 171905.png
2026-05-04 Rename mec/chassi_superior.FCStd to mec/modelagem 3d/superior/chassi_superior.FCStd
    [chassi_superior.FCStd]
2026-05-04 Rename mec/Base.FCStd to mec/modelagem 3d/base/Base.FCStd
    [Base.FCStd]
2026-05-04 Rename mec/Captura de tela 2026-05-03 205549.png to mec/modelagem 3d/base/Captura de tela 2026-05-03 205549.png
2026-05-04 feat: integracao dos motores e da ponte h
2026-05-04 docs: adicao dos datasheets do motor e da ponte h
2026-05-04 docs: criacao da documentação sobre metodos de transmissão da roda no motor
2026-05-04 feat: organização de diretórios e classe do sensor de distância
2026-05-04 docs: corrigindo falta de informação
2026-05-04 feat: desenvolvimento de classe pro firmware do imu
2026-05-04 docs: cálculo da capacidade mínima que a bateria deve possuir
2026-05-04 fix: adiciona autor dos artefatos, histórico de versão e corrije erros no documento.
2026-05-04 git commit -m "docs: adiciona orçamento e seleção de componentes para o sistema de baterias
2026-05-04 docs(paredes): adicionar cad da parede interna
    [Parede_interna_junta_asa.CATPart]
2026-05-04 docs: adiciona DER e MER à pagina de arquitetura de software.
2026-05-04 docs(carcaça): adicionar cad da parede externa
    [Parede_externa_junta_asa.CATPart]
2026-05-04 docs(carcaça): adicionar cad das juntas das paredes
    [Junta_L.CATPart, junta_4_internas.CATPart]
2026-05-04 fix: adiciona revisor ao histórico de versão
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2026-05-05 fix: compatibilidade de bibliotecas
2026-05-05 fix: adequação de firmware -arduino.h
    [example.c, imu.cpp, imu.h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]
2026-05-05 fix: adição de componentes ao REQUIRES do CMakeList.txt da Main
2026-05-05 docs: adiciona diagrama lógico de dados ao documento de arquitetura de software.
2026-05-05 docs: adiciona os revisores ao histórico de versão
2026-05-05 fix: muda atriubutos de labirinto e corrida no DER e DLD
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2026-05-06 docs: Escolha do IMU e sensor de corrente
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2026-05-06 fix: estrutura da sidebar de software
2026-05-06 docs: add documentação de rodas e transmissão nas pages
2026-05-06 feat: unifica sensores, motores e gravação SD
    Logica completa do vl53l0x ainda não foi definida(como vamos usar os 4 sensores ao mesmo tempo), então código ainda não tem essa parte
2026-05-06 docs(energia): Adiciona documentação do sistema de carregamento da bateria
2026-05-07 docs: criação do documento incial para os casos de teste do software
2026-05-08 docs(carcaca): adicionar motor, bateria e furo de sensores
    [Base-2.2.FCStd]
2026-05-09 docs:. adiciona visao de processos diagrama de sequencias
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2026-05-09 docs(latexEnergia): Remove relatorio .tex da pasta de energia
    Iremos adicionar nossas mudanças direto no arquivo que está em docs/relatorio/relatorio.tex
2026-05-10 feat(base): adicionar cad com suporte motor, bateria, sensores
    [Base-2.4.FCStd]
2026-05-10 Merge pull request #162 from fcte-pi1/add-lista-componentes-estrutura
    docs(chassi): Adicionar lista de componentes para estrutura
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2026-05-10 feat(chassi): adicionar cad do suporte do motor e do sensor separados
    [SuporteMotor1.0.FCStd, SuporteSensor1.0.FCStd]
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2026-05-10 fix(chassi): consertar medida interna de chassi superior
    [chassi_superior3.0.FCStd]
2026-05-10 fix: Esquemático PCB
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2026-05-10 docs: Revisão estrutural da arquitetura e integração completa das visões de hardware e software embarcado
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2026-05-11 docs: add modelagem cad da roda e pneu
    [Roda-1.0.FCStd]
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2026-05-11 move o documento de arquitetura para a pasta pages/docs/software e corrije erro 404 na sidebar backlog do produto
2026-05-11 refactor(labirinto): mudar local dos arquivos cad
    [Junta_L.CATPart, Parede_externa_junta_asa.CATPart, Parede_interna_junta_asa.CATPart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]
2026-05-11 docs(labirinto): adicionar 3d do piso
    [Labirinto06.FCStd]
2026-05-11 docs: Lista de materiais da PCB
    Lista de materiais criado pelo próprio easyeda
    [BOM_Board1_Schematic1_2026-05-11.xlsx]
2026-05-12 docs: colocando cads da engrenagem
    [ENGRENAGEM_MAIOR.FCStd, ENGRENAGEM_MENOR.FCStd]
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2026-05-13 fix: ajustar tabelas de versionamento de estrutura
2026-05-13 fix: ajuste de sidebar para estrutura/roda
2026-05-13 docs(chassi): adicionar modelo 3d do skid deslizador
    [Skid1.0.FCStd]
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2026-05-16 test: testes para validar funcionamento do websocket e alteração no dockerfile para suportar os testes.
2026-05-16 task: Adição de websocket, rotas e shcemas de telemetria e alteração nas models com realização de migrations.
2026-05-16 corrige nome de campos e adiciona docstring a model
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2026-05-17 adiciona envio de dimensao do labiritno e numero da tentavia pelo websocket
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
